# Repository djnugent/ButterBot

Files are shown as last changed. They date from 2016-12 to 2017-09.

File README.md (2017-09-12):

# Butterbot
---
##### Video
Video (https://youtu.be/BhRFnhcuLr8)

## TL;DR

While [working with Jamie at M5 Industries](http://danielnugent.com/m5-industries-proj.html) I set out to diversify my skill set and embarked on a mechanically oriented project.  If you have read my other write up about my summer at M5 industries you will know that I was simultaneously working on a software robotics project, and I wanted a project which focused on mechanical design and fabrication. Butterbot strictly exists as a fictional character from the show Rick and Morty, so I set out to make him a real robot.

## Shell

parts

Butterbot’s body is mostly made of aluminum. 5 sides of his head are made of bent sheet metal with his face being made of machined aluminum plate. His base and neck are made of machined aluminum stock. All other parts are made from acrylic, plastics, wire, and various do-dads. All parts are secured using pressure fitting, welding, bolts, or epoxy.

## Motion

motion

Butterbot contains 5 actuators:
- 2 variable speed track elements at his base
- 2 micro servo motors in his shoulders
- 1 mini servo motor at the base of his head for his main neck joint

This doesn’t seems like that much, but it was a lot to fit into a small form factor. The motors and gearbox for the track elements take up 7/8 of the space in the base. Only leaving just enough room for a dual h-bridge motor controller and small battery. The shoulder servos took up 2/3 of the width of his head, making it extremely hard to place all the electronics and neck servo.

## Neck

neck

Butterbot’s neck was the hardest part of this build so I felt it required its own section. As you can see Butterbot’s neck is way too small to fit an actuator inside of it so the servo motor had to be placed in his head. In addition to his head being tight on space, it was heavy as a result of electronics, motors, arms, and its size. The force it exerted on the neck joint was multiplied by that fact that the upper joint of his neck acted as a 4in lever.  So what I had to design was a small yet high torque head mounted system which transferred energy to his neck. This was achieved using a cable/pulley system and a high torque servo (highest torque you can buy in the mini servo category). The servo was mounted at the base of the head with its output shaft running parallel with his base (perpendicular to the neck joint shaft). This 90 degree offset was due to the limited space in the head. This meant the pulley cables had to twist 90 degrees as they traveled down his neck. In order to prevent the cables from slipping on the pulleys, the cables were crimped onto the pulleys. Keep in mind these pulleys were only 0.5in in diameter. Adding cable crimping wasn’t easy. The biggest issue was that after the 4in neck, heavy head, and small pulley the resulting force on the cable was roughly 22lbs! I had to go through many iterations of pulley designs, cable types, and crimping methods so that the cable wouldn’t slip or snap. What should have taken 3 days took 2 weeks.

## Electronics

electronics

Butterbot is packed with cool features. He contains:
- Wifi enabled microcontroller(Particle Photon)
- A programmable sound card(Adafruit)
- ~~D class mono audio amplifier(Adafruit)~~ Lm386 Mono Amp(Amazon)
- ~~3 watt speaker~~ HTC M8 One speaker
- Dual h-bridge serial motor controller(Polulo)
- ~~2 amp voltage regulator~~ 3 amp LT1764A voltage regulator
- ~~Face tracking Camera (OpenMV)~~
- LED

Everything but the motor controller fits in his head. He is wired with 3 different voltage levels (3.3v, 5v, 8v). He runs off a 2 cell 300mah battery. He has the ability to talk, track your face*, and move. ~~The camera used to fit in the head, but the audio amplifier wasn’t loud enough so I had to add a larger speaker in place of the camera. If I get a better amplifier(that’s the same size) then I should be able to put the camera back in(which I really want to do considering I already programmed it!)~~  I upgraded the speaker system and the camera fits again! Update: I didn't own the camera and the owner took it back....right as I got it working.

## [App](https://github.com/djnugent/butterbot-app)

app

Butterbot is controlled over wifi using an android app. The app allows me to drive him, play audio clips, track faces, and monitor battery level. It communicates with the microcontroller using TCP sockets. Below you can find some gifs of UI functionality.

## Microcontroller

electronics

The microcontroller manages all his electrical systems and makes sure he operates smoothly. He is mechanically unstable(top heavy) so filters and constraints are in place so he doesn’t wreck himself. The microcontroller runs an realtime operating system(RTOS) so it uses threading and system timers to handle continuous filtering and task scheduling. It also has built in wifi so it acts as TCP server and also communicates with a cloud server to send connection credentials to the app. If butterbot can’t connect to the local network he will setup a wifi spot so his network setting can be reconfigured(like a chromecast).

## Problems
I had some unexpected electrical problems along the way. First his speaker wasn’t loud enough. I tried to fix this with a larger speaker, but that barely helped and caused me to remove the camera due to space constraints. I eventually settled for a new amp and an HTC M8 speaker(best I could find). This allowed for the camera to be put back in.

Next his neck would glitch when not enabled(no PWM). It’s not enabled on power up because he needs to be upside down to plug in his battery. This was fixed by grounding the servo signal line with a 10k resistor.

After that, the arm servos would cause a voltage drop on the 5v line and it would reboot the audio card and microcontroller. This was frustrating because the servos were really nice but drew too much current during acceleration. This was fixed by designing a 5v regulator with a fast transient response based on the LT1764A.

Finally, the most troubling issue I encountered was the motor controller for the base would lock up randomly when the neck was enabled. It required a full reset in order to get it operational again. It was completely undocumented behavior for the controller(which was essentially a microcontroller with dual HBridge). It was really strange. At first I thought the issue was caused by PWM noise from the neck servo leaking into the serial line of the motor controller. But after poking and prodding and causing butterbot to drive off the table and BREAK HIS NECK! I figured out that the cheap hobbyking neck servo, that was powered in parallel with the motor controller, was creating noise on the power lines(which are supposedly isolated from the TTL power). Apparently the isolation wasn’t good enough and the power noise caused the microcontroller to brick. I fixed this by putting a 100uF capacitor across the main power lines. Long story short hobby king servos suck. They had noise issues on their signal and power lines.

The only major software problems I encountered was a TCP delay issue which I solved by forcing TCP to send packets when they were ready, not when they hit 1500 bytes. Additionally, I had trouble programming the photon to go into configuration mode when it couldn’t connect to the specified wifi network. This was caused by lack of documentation and solved by trial and error.

## Additional Photos

Visit my official [write up](http://danielnugent.net/butterbot-proj.html)

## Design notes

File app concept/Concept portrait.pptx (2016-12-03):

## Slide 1

Butterbot

Connecting…

Created By Daniel Nugent

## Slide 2

Butterbot

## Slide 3

Butterbot

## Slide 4

Butterbot

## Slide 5

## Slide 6

Butterbot

Oh my God

Purpose

Friendship

Beep

Boop

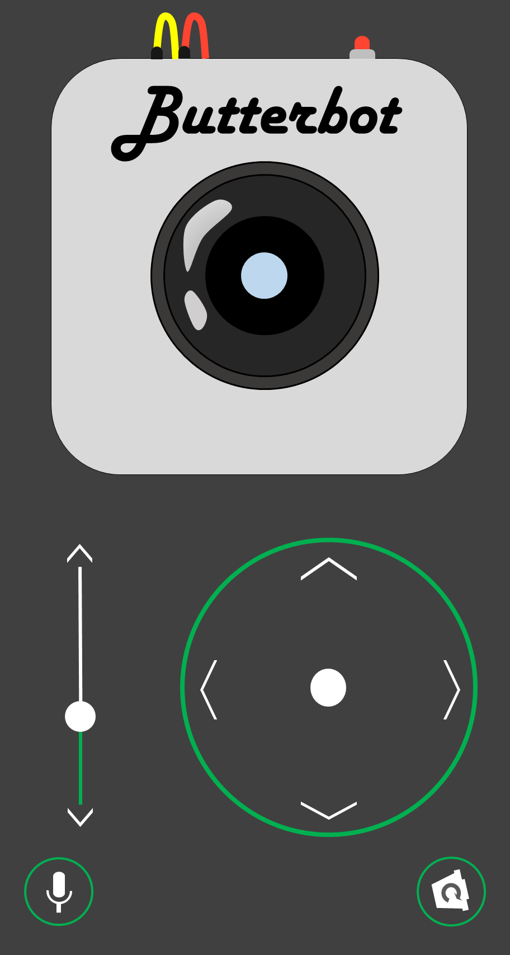
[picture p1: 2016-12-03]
app concept/Slide5.PNG

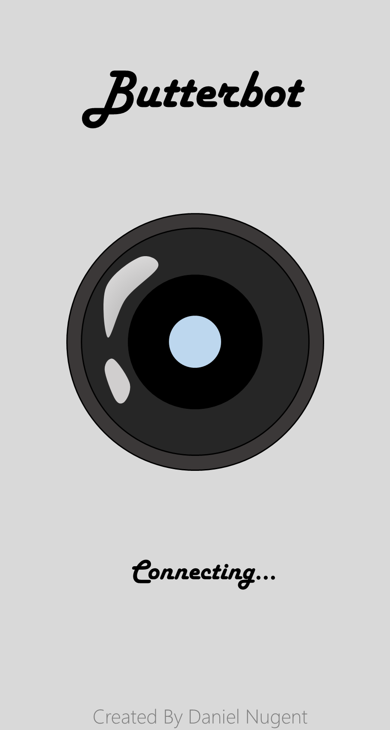
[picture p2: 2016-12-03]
app concept/Slide2.PNG

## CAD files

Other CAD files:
CAD/Neck.skp
CAD/butterbot.skp
CAD/butterbot2.skp
CAD/butterbot_head.skp

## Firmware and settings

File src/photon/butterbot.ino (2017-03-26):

#include "LED.h"
#include "Audio.h"
#include "Treads.h"
#include "SmoothServo.h"
#include "define.h"
#include "Safe_Connect.h"
#include "Serial2/Serial2.h"

//////////DO NOT CHANGE////////////
SYSTEM_THREAD(ENABLED);  //Allows for special wifi config DURING setup
SYSTEM_MODE(SEMI_AUTOMATIC); //Allows for custom wifi
//////////DO NOT CHANGE////////////

//LED
LED led;

//Servo
SmoothServo armR;
SmoothServo armL;
SmoothServo neck;

//Treads
Treads base;

//sound
Audio speaker;


//battery
int batt_level = 1000;
int batt_low = 0;
int last_batt_check = 0;

//TCP server
TCPServer server = TCPServer(TCP_PORT);
TCPClient client;
int just_connected = true;
int last_publish = 0;
int last_packet = 0;
int last_heartbeat = 0;

//timer to update servos
Timer servo_timer(int(1000/SERVO_UPDATE_RATE), update_servos);
//Timer to update treads
Timer base_timer(int(1000/TREADS_UPDATE_RATE), update_base);



void setup() {

    //USB debug
    Serial.begin(115200);

    //Sound card
    speaker.init(9600);

    //Init base
    base.attach(38400,-100,100);
    base.set_params(1, 0);

    //LED
    led.init(LED_PIN);

    //battery
    pinMode(BATT_PIN,INPUT);

    //attach the servos
    armR.attach(RIGHT_ARM_PIN,1000);
    armL.attach(LEFT_ARM_PIN,2000);

    //limit their speeds
    armR.set_max_us_per_sec(4000);
    armL.set_max_us_per_sec(4000);
    neck.set_max_us_per_sec(500);

     //Set range limits
    armR.set_limits(1000,2000);
    armL.set_limits(1000,2000);
    neck.set_limits(1100,1900);


    //Start timers
    base_timer.start();
    servo_timer.start();

    //connect to the network or start our own
    safe_connect();

    //start TCPServer for app
    server.begin();
}

void loop() {

  //check for commands
  check_tcp();
  check_usb();

  //update LED
  led.update();

  //check battery
  check_battery();

}


void update_servos(){
    armL.update();
    armR.update();
    neck.update();
}

void update_base(){
    base.update();
}


//Get commands from the app
void check_tcp(){
  if (client.connected()) {
    //modify state of led upon connection
    if(just_connected){ //stop led breathing when we connect
        led.set_LED(LED_MODE_TALK,0);
        just_connected = false;
        last_packet = millis();
    }

    //Process incoming data
    if(client.available() >= PACKET_SIZE) {
        last_packet = millis();
        byte raw[PACKET_SIZE];
        client.read(raw,PACKET_SIZE);
        process_command(raw,SRC_TCP);
        //server.write(raw,PACKET_SIZE);
    }
    //check for client disconnect
    else if(millis()-last_packet > TCP_TIMEOUT){
        client.stop();
        speaker.play(0,&led);
    }
  }//Wait for connection from app
  else {
        //Broadcast our connection status every 1.5 seconds
        if(millis()-last_publish >1500){
            String connection_info = "";
            connection_info.concat(WiFi.SSID()); //SSID
            connection_info.concat(":");
            connection_info.concat(String(WiFi.localIP())); //IP
            connection_info.concat(":");
            connection_info.concat(String(TCP_PORT)); //TCP Port
            Particle.publish("ConnectionInfo", connection_info,0,PRIVATE);
            last_publish = millis();
        }
        // if no client is yet connected, check for a new connection
        client = server.available();

        //put butterbot in resting state if we went from connected to disconnected
        check_battery();
        if(batt_low){
            led.set_LED(LED_MODE_BATT,0);
        }
        else{
            led.set_LED(LED_MODE_CNCT,0);
        }
        armL.set_us(2000);
        armR.set_us(1000);
        neck.detach();
        base.set_motors(0,0);
        just_connected = true;
  }
}

//Get commands from USB
void check_usb(){
    if(Serial.available() >= PACKET_SIZE) {
        byte raw[PACKET_SIZE];
        for(int i = 0; i < PACKET_SIZE; i++){
            raw[i] = Serial.read();
        }
        //Serial.write(raw,PACKET_SIZE);
        process_command(raw,SRC_USB);
    }
}

void check_battery(){
    if(millis()-last_batt_check > BATT_CHECK_RATE){
        batt_level = int(analogRead(BATT_PIN)*BATT_ALPHA + batt_level*(1 - BATT_ALPHA)); //Exp average
        batt_low = batt_level < BATT_MIN;

        //flash led on low battery
        if(batt_low){
            led.set_LED(LED_MODE_BATT,0);
        }
        last_batt_check = millis();
    }
    if(!just_connected && millis()-last_heartbeat > 200){
      byte cmd[PACKET_SIZE] = {BATT_LVL,0,0,0,0,'\n'};
      cmd[1] = (batt_level & 0xff00) >> 8; //msb
      cmd[2] = batt_level & 0x00ff; //lsb
      cmd[3] = (batt_low & 0xff00) >> 8; //msb
      cmd[4] = batt_low & 0x00ff; //lsb
      server.write(cmd,PACKET_SIZE);

      last_heartbeat = millis();
    }


}


//Process commands from TCP/USB client
void process_command(byte *buffer, int cmd_src){

    char cmd = buffer[0];
    int arg1 = buffer[1] << 8 | buffer[2];
    int arg2 = buffer[3] << 8 | buffer[4];

    switch(cmd){
        case CTRL_MOTORS:{
            base.set_motors(arg1-255,arg2-255);
        break;}
        case CTRL_ARMS:{
            armL.set_us(arg1);
            armR.set_us(arg2);
        break;}
        case CTRL_NECK:{
            neck.set_us(arg1);
        break;}
        case CTRL_LED:{
            led.set_LED(arg1,arg2);
        break;}
        case CTRL_AUDIO:{
            speaker.play(arg1,&led);
        break;}
        case CTRL_LIST_MODE:{
            listen();
        break;}
        case BATT_LVL:{ //Send battery level
          /*
            byte cmd[PACKET_SIZE] = {BATT_LVL,0,0,0,0,'\n'};
            cmd[1] = (batt_level & 0xff00) >> 8; //msb
            cmd[2] = batt_level & 0x00ff; //lsb
            cmd[3] = (batt_low & 0xff00) >> 8; //msb
            cmd[4] = batt_low & 0x00ff; //lsb
            if(cmd_src == SRC_TCP){
                server.write(cmd,PACKET_SIZE);
            }
            else if(cmd_src == SRC_USB){
                Serial.write(cmd,PACKET_SIZE);
            }
            */
            break;}
        case ATTACH_NECK:{
            if(arg1 == 0){
                //neck.set_us(1100);
                //delay(1500);
                neck.detach();
            }
            else if (arg1 ==1){
                neck.attach(NECK_PIN,1050);
            }
            break;}
        default:{ //Invalid Command
            byte cmd[PACKET_SIZE] = {CMD_ERROR,0,0,0,0,'\n'};
            if(cmd_src == SRC_TCP){
                server.write(cmd,PACKET_SIZE);
            }
            else if(cmd_src == SRC_USB){
                Serial.write(cmd,PACKET_SIZE);
            }
        break;}
    }
}

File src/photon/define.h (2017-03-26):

#ifndef DEFINE_H__
#define DEFINE_H__

#define WIFI_TIMEOUT    5000        //5 seconds
#define TCP_TIMEOUT     2000        //1.5 second of app disconnecting
#define PACKET_SIZE     6           //byte(1) + int(2) + int(2) + NL(1)
#define TCP_PORT        88          //TCP port for app

//Commands
#define CMD_ERROR       0x00        //Invalid command
#define CTRL_MOTORS     0x01        //control treads        - {Left(0,511),right(0,511)} offset 255 aka 255 ->0
#define CTRL_ARMS       0x02        //control arms          - {Left(1000,2000),right(1000,2000)}
#define CTRL_NECK       0x03        //control neck          - {(1000,2000)}
#define CTRL_LED        0x04        //control LED           - {LED_MODE, On/Off or blink_ms}
#define CTRL_AUDIO      0x05        //play sound track      - {AUDIO}
#define CTRL_LIST_MODE  0x06        //activate listen mode  - {}
#define BATT_LVL        0x07        //Battery Level
#define ATTACH_NECK     0x08        //Activate the neck     - {0/1}

//Sources
#define SRC_USB         0           //Commands came from USB
#define SRC_TCP         1           //Commands came from TCP

//PINS
#define LEFT_ARM_PIN    A5
#define RIGHT_ARM_PIN   WKP
#define NECK_PIN        A4
#define LED_PIN         A3
#define BATT_PIN        A2

//Battery
#define BATT_CHECK_RATE 100
#define BATT_ALPHA      0.1
#define BATT_MIN        845         //6.4v on a 0 - 4096 scale. digital = 137.7*(voltage) - 53

#endif

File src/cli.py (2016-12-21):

import serial
import struct
import socket
import time
import threading
import traceback
import sys
import argparse



######Command Line interface for testing butterbot over USB/TCP#####################



class butterbot():

    CMD_ERROR      = 0x00        #Invalid command
    CTRL_MOTORS    = 0x01        #control treads        - {Left(-255,255),right(-255,255)}
    CTRL_ARMS      = 0x02        #control arms          - {Left(1000,2000).right(1000,2000)}
    CTRL_NECK      = 0x03        #control neck          - {(1000,2000)}
    CTRL_LED       = 0x04        #control LED           - {LED_MODE, On/Off or blink_ms}
    CTRL_AUDIO     = 0x05        #play sound track      - {AUDIO}
    CTRL_LIST_MODE = 0x06        #activate listen mode  - {}
    BATT_LVL       = 0x07        #Battery Level
    ATTACH_NECK    = 0x08        #Activate the neck
    OPENMV_ENABLE  = 0x09        #Enable OpenMV tracking- {0/1}
    OPENMV_POS     = 0x0A        #OpenMV position packet


    LED_MODE_TALK   = 0x00        #Flash LED while talking
    LED_MODE_BLINK  = 0x01        #Flash at a continous rate
    LED_MODE_IO     = 0x02        #LED either on or off
    LED_MODE_CNCT   = 0x03        #LED breathes while waiting for the app to connnect
    LED_MODE_BATT   = 0x04        #LED flashes fast when battery is low


    def __init__(self):
        self.ser = None
        self.tcp = None
        self.batt_level = None
        self.stream_camera = False
        #request battery status
        t = threading.Thread(target=self.check_battery)
        t.start()
        #parse incoming data
        t1 = threading.Thread(target=self.recv_command)
        t1.start()


    def start_serial(self,port,baud):
        self.ser = serial.Serial(
            port=port,
            baudrate=baud,
            timeout=0.1
        )
        self.ser.reset_input_buffer()

    def start_tcp(self,server,port):
        # Create a TCP/IP socket
        self.tcp = socket.socket(socket.AF_INET, socket.SOCK_STREAM)
        self.tcp.connect((server, port))


    def send_command(self,cmd_id, arg1, arg2):
        cmd = struct.pack(">bhhc",cmd_id,arg1,arg2,b'\n')
        if(self.ser is not None):
            self.ser.write(cmd)
        if(self.tcp is not None):
            self.tcp.send(cmd)

    def recv_command(self):
        time.sleep(1)
        while(True):
            raw = []
            if(self.ser is not None):
                raw = self.ser.read(6)
            if(self.tcp is not None):
                raw = self.tcp.recv(6)
            if(len(raw) == 6):
                cmd_id = raw[0]
                arg1 = (raw[1] << 8) | raw[2]
                arg2 = (raw[3] << 8) | raw[4]
                if(cmd_id  == self.BATT_LVL):
                    self.batt_level = arg1
                elif(self.stream_camera and cmd_id == self.OPENMV_POS):
                    print(arg1,arg2)
                else:
                    print((hex(cmd_id),arg1,arg2,raw))

    def check_battery(self):
        while(True):
            self.send_command(self.BATT_LVL,0,0)
            time.sleep(0.15)

    def close(self):
        if(self.ser is not None):
            self.ser.close()
        if(self.tcp is not None):
            self.send_command(self.OPENMV_ENABLE, 0,0)
            self.tcp.close()




if __name__ == "__main__":


    bb = butterbot()

    parser = argparse.ArgumentParser(description='Command line interface for testing butterbot')
    parser.add_argument('connection_string', action="store", help="Serial port or IP address")
    parser.add_argument('--baud', default=115200, help="Serial port baud")
    parser.add_argument('--port', default=88, help="TCP port")
    args = parser.parse_args()

    #TCP connnection
    if(args.connection_string.count('.') == 3):
        bb.start_tcp(args.connection_string,args.port)
        print("Connected on {}:{}".format(args.connection_string,args.port))
    #Serial Connection
    else:
        bb.start_serial(args.connection_string,args.baud)
        print("Connected on {}:{}".format(args.connection_string,args.baud))

    #run a CLI for managing users
    exit = False
    while not exit:
        try:
            time.sleep(0.1)
            cli = input('>>>').split()
            if len(cli) > 0:
                cmd = cli[0]
                if cmd == "help":
                    print("CLI for butterbot")
                    print("    base   [throttle] or [left thr] [right thr]      #controls base")
                    print("    arm   [us] or [left us] [right us]               #controls arms")
                    print("    neck  [us]                                       #controls neck")
                    print("    led   on/off/talk/batt/connect/blink{blink rate} #controls led")
                    print("    play  [track number]                             #plays audio")
                    print("    batt                                             #displays battery status")
                    print("    listen                                           #put photon into listen mode")
                    print("    exit                                             #exit CLI")

                elif cmd == "base": #base
                    if len(cli) == 2:
                        bb.send_command(bb.CTRL_MOTORS,int(cli[1]) + 255,int(cli[1])+255)
                    elif len(cli) == 3:
                        bb.send_command(bb.CTRL_MOTORS,int(cli[1]) + 255,int(cli[2])+255)
                    else:
                        print("invalid usage")

                elif cmd == "arm": #arms
                    if len(cli) == 2:
                        bb.send_command(bb.CTRL_ARMS,int(cli[1]),int(cli[1]))
                    elif len(cli) == 3:
                        bb.send_command(bb.CTRL_ARMS,int(cli[1]),int(cli[2]))
                    else:
                        print("invalid usage")

                elif cmd == "neck": #neck
                    if len(cli) == 2:
                        if cli[1] == 'enable':
                            bb.send_command(bb.ATTACH_NECK,1,0)
                            bb.send_command(bb.CTRL_NECK,1500,0)
                        elif cli[1] == 'disable':
                            bb.send_command(bb.ATTACH_NECK,0,0)
                        else:
                            bb.send_command(bb.CTRL_NECK,int(cli[1]),0)
                    else:
                        print("invalid usage")
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

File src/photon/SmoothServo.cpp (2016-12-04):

#include <Particle.h>
#include "SmoothServo.h"


void SmoothServo::attach(int pin, int start_us){
  if(!attached){
      ser.attach(pin);
      ser.writeMicroseconds(start_us);
      current_us = start_us;
      target_us = start_us;
      attached = true;
  }
}

void SmoothServo::detach(){
    ser.detach();
    attached = false;
}

void SmoothServo::set_max_us_per_sec(int mups){
  max_us_per_sec = mups;
}

void SmoothServo::set_limits(int mi, int ma){
  min_us = mi;
  max_us = ma;
}

void SmoothServo::set_us(int us){
    target_us = us;
}

void SmoothServo::update(){
    int thres = max_us_per_sec * 1.0/SERVO_UPDATE_RATE;
    if(target_us <= max_us && target_us >= min_us){
        int diff = target_us - current_us;
        current_us += min(max(diff,-thres),thres);
    }
    ser.writeMicroseconds(current_us);
}

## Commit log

2017-01-06 Minor fixes and increased OpenMV support
    [Treads.cpp, Treads.h, butterbot.ino]
2017-03-26 Fixed network issue, force feed battery levels as heartbeat
    [butterbot.ino, define.h]
